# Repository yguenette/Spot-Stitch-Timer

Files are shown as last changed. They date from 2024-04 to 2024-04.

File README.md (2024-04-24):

# Spot-Stitch-Timer
Spot and Stitch Timer is a module to control the Miller Multimatic 215 Welder

## The module

To help weld thin metal (20, 22 and 24 AWG) and to maintain a minimal heat affected zone, it is important to find the right combination of voltage, WFS (wire feed speed), distance and trigger "on" time to eliminate the possibility of through holes or under welding. The key is to practice on similar metal pieces on a bench in ideal conditions where experimentation is possible. The voltage and WFS are pre-determined by the welder and can be fine tuned by the user - they are dialed in. Once programmed, these values will remain constant until they are changed. The nozzle distance to object is controllable by the user and more or less repeatable. The last variable (trigger ON time) is harder to reproduce since the position, the posture and the shear number of welds can make it difficult to maintain/repeat consistently. This is where a spot timer comes in. Once programmed with a spot ON time, it will remain the same until changed by the user. Having the flexibility of adding a delay time before the spot weld ON time will allow the user to press/release the trigger, before the weld starts and have a more stable position for the weld.

The spot/stitch timer module controls the welder with very specific welding time that will help with reproducibility of the welds. By dialing in the voltage, WFS, distance and weld time, we are closer to achieving repeatable welds.

This module (Raspberry Pi Pico and a 4 channels relay board) is packaged in a 3D printed box. This box sits inside the welder - in the same compartment as the wire spool - between the trigger torch and the welder. This module has 4 mode of operations. They are:

	1.  **Unpowered-Normal** : In this mode (default) the torch's trigger is passed through to the welder.
	2.  **Powered-Normal** : In this mode (default) the torch's trigger is passed through to the welder.
	3.  **Powered-Spot** : In this mode, the torch's trigger is isolated from the welder and sensed by the spot/stitch timer module. The Spot weld-time is programmable: delay and the spot weld ON time are specified. Each time the trigger is pressed/released, the module will create a combination Delay/Spot weld ON sequence;
	4.  **Powered-Stitch** : In this mode, the torch's trigger is isolated from the welder and sensed by the spot/stitch timer module. The Stitch ON/OFF weld-time is programmable: delay and the stitch weld ON/OFF time are specified. This sequence weld-ON/weld-OFF is repeated until the trigger is pressed/released again.

## The control software (interface):

When powered, the spot/stitch timer module will default to normal mode. The module can be controlled via Bluetooth using a android smartphone. The Android program used to communicate with the spot/stitch timer module is called: Serial Bluetooth Terminal, and is available through the app store.

Once connected, there are 6 pre-program functions and 2 commands supported. 

The 6 pre-programmed functions are:

	1.  **normal** : This programs the powered module to return to normal mode;
	2.  **mode?** : This sends a command to the module asking to report the present mode of operation. The possible response is:
		a. normal;
		b. spot;
		c. stitch;
	3.  **prog?** : This sends a command to the module asking to report the programmed delay, On and Off (only for stitch mode) for both spot and stitch modes;
	4.  **temp?** : asking the raspberry pi pico for its internal temperature. Normal temperature that I have seen range from 26C to 39C. The specification for the pico is : Max = +70C, Min = -20C.
	5.  **count?** : This reports the number of spot welds performed in this session and the number of stitch welds in this session;
	6.  **help** : reports the format of the 2 additional commands. They are:
		a. Spot delay ON
		b. Stitch delay ON OFF

The 2 commands supported are:

	1. spot <delay> <ON>
	2. stitch <delay> <ON> <OFF>

Looking at the Serial Bluetooth Terminal application, we can connect with the module by pressing the symbol on the second line from the top, third from the left.

The spot/stitch supported commands are typed on the bottom line. The command is send by pressing the icon on the right side of that line.

Screenshot_20240423_170638_Serial Bluetooth Terminal

## The final product



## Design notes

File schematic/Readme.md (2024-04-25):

# Schematic directory structure

Tool used for the schematic capture is KiCad

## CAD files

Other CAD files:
3D-Print-files/Cover FINAL.f3d
3D-Print-files/Languette Light FINAL.f3d
3D-Print-files/box_85x85mm FINAL (CURRENT).f3d
3D-Print-files/protective plate FINAL.f3d

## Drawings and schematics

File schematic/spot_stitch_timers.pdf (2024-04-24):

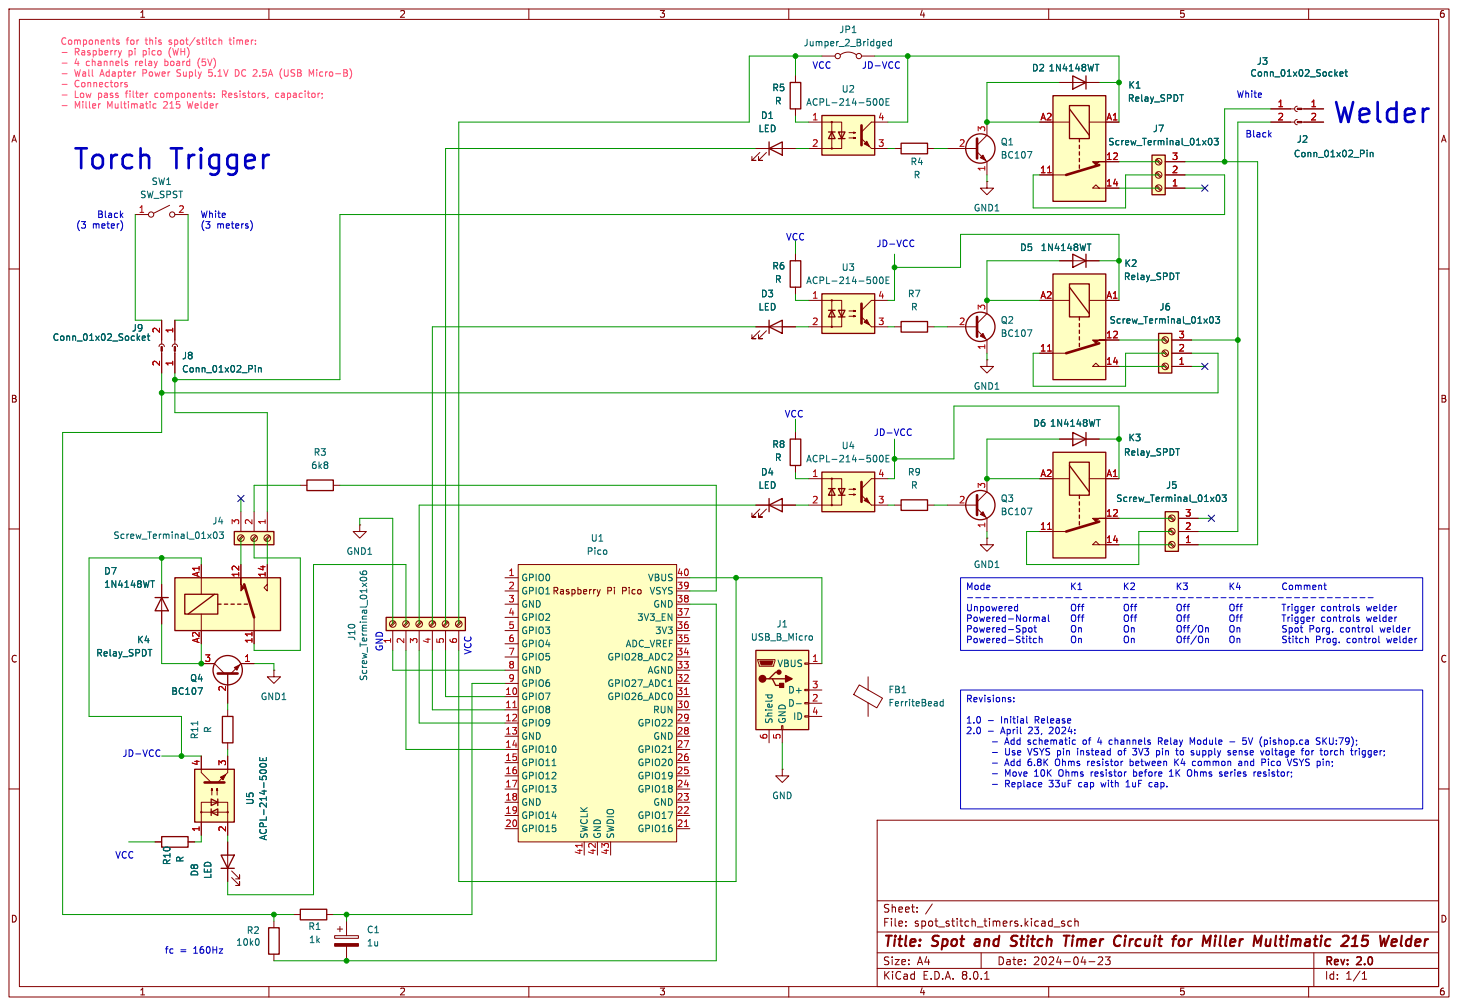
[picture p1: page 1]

- Wall Adapter Power Suply 5.1V DC 2.5A (USB Micro-B)
- Connectors
Torch Trigger

Id: 1/1 Title: Spot and Stitch Timer Circuit for Miller Multimatic 215 Welder File: spot_stitch_timers.kicad_sch Sheet: /

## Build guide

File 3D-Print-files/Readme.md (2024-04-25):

# Description:

directory structure added for the 3D printed files.

Tool used: Fusion360

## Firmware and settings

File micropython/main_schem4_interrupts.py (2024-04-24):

#-------------------
# YAG:
#
# Code to start and monitor the Bluetooth LE (BT) function and monitor the welder trigger.
#   At the time of this writing (March 2024), the dual core functionality was
#   attempted but not successful while using BT. It was however dual core was functional while using simple
#   functions like LED blinking and counter exercises.
#
# All programs are modified via the BT interface. The Android application that I used is called:
#
#   Serial Bluetooth Terminal
#
#
# The steps in this program are:
#
#	1) Initialize the relays so that the circuit operates in "Normal" mode by default;
#       To be clear, after further investigation of bouncing with the Miller torch
#       - pressing the trigger causes between 11 and 15 bounces with a duration of worst case,
#       seen of 235ms (with 4.7kOhms pull-down), while the release of the trigger causes very
#       little bounces at all.
#       In the 'normal' mode, I decided to bypass the controller altogether and passthru the
#       miller trigger directly to the welder. Note that the welder likely has (internally)
#       a debouncing circuit. In this mode the relays are all in their OFF position.
#	2) When the trigger is activated, the program will determine if the mode of operation is:
#		a) NORMAL - trigger passthru directly to welder;
#		b) SPOT - trigger on/off is determined by the spot welder programmed duration;
#		c) STITCH - trigger on/off is determined by the stitch programmed ON time followed by
#			the programmed OFF time - repeat as long as the trigger remains ON.
#
# If the microcontroller is un-powered, the relays will be positioned to allow the trigger to
#   be passed on to the welder.
#
# 1.0.0 - Initial version. March 26, 2024
#			- Allow bluetooth communication
#
# 5.0.0 - Now using V3 of the schematic - see green book for more details.
#       - Two (2) major changes done to the schematic:
#           - 1) Relay 3 was simplified so that Common pole and NO (Normally Open) pole are
#                  connected to the outputs of the relay 1 and 2 (Normally Closed poles).
#
#           - 2) Relay 4 is now used to disconnected the 'white' trigger wire from the pin 4 of
#                  the RPI-PICO. When the RPI-PICO is un-powered, the voltage at that pin is 17.7V
#                  That has the potential to destroy the PICO.
#
# 6.0.0 - Now using version 4 of the schematic. In this version, the "pwr_3v3_meas" pin is now connected
#         to the 3V3 power pin (3.3V). This means that wire on pin 4 is moved to pin 36.
#         Also, pin 34 is now jumpered to GND (pin 38).
#         From a programming point of view, these 2 pins (GPIO28 (pin 34) and GPIO2 (pin 4)) are now
#         GPIO input pins.

#
# future work:
#
#-------------------------------
# Import necessary modules
import _thread, utime
from machine import Pin, mem32
import bluetooth
from ble_simple_peripheral import BLESimplePeripheral

bounce_delay = 0.1
relay_switching = 0.1

# Backend GPIO pin definitions
# --------------------------------
relay_1 = machine.Pin(7,machine.Pin.OUT) #Relay 1 control. Turn ON by forcing 0V.
relay_2 = machine.Pin(8,machine.Pin.OUT) #Relay 1 control. Turn ON by forcing 0V.
relay_3 = machine.Pin(9,machine.Pin.OUT) #Relay 1 control. Turn ON by forcing 0V.
relay_4 = machine.Pin(10,machine.Pin.OUT) #Relay 1 control. Turn ON by forcing 0V.

# Relay control section (initializtion/default settings). Backend:
#------------------------------------------------------------------
# Control the GPIO pins to the correct default states
led_state = 0 # PICO green LED. Default state is OFF
relay_1_state = 0 # Relay 1 control state. Default is OFF - used for the passthru of the white wire
relay_2_state = 0 # Relay 2 control state. Default is OFF - used for the passthru of the black wire
relay_3_state = 0 # Relay 3 control state. Default is OFF - this relay is only controlled during SPOT and STITCH modes.
relay_4_state = 0 # Relay 4 control state. Default is OFF

relay_1.value(not relay_1_state)
relay_2.value(not relay_2_state)
relay_3.value(not relay_3_state)
relay_4.value(not relay_4_state)

utime.sleep(relay_switching) # Wait for the relays to settle.

# Frontend GPIO pins to use for the switch sensing
#---------------------------------------------------------
#This output is used to drive a fixed level. Between this output (pwr_3v3_meas) and the sensing input (sw_in), there is relay4 (default off)
#   and the trigger of the welder.
# pwr_3v3_meas = machine.Pin(2,  machine.Pin.IN) #This is now connected to 3.3V
sw_in    = machine.Pin(6,  machine.Pin.IN) #other side of the switch. Input. Pull-up of 4.7K provided externally. The other side of this PD is another GPIO (28)
# gnd_meas = machine.Pin(28, machine.Pin.IN) # GPIO pin used as a GND when in SPOT and STITCH modes only. Else input floating,
sw_in.irq(handler=None)  # disable interrupt during the switching of relay4. It creates an interrupt.

# Temperature sensor initialization
#------------------------------------------
adcpin = 4
sensor = machine.ADC(adcpin)


#Global variables:
normal = 1
spot = 0
spot_delay = 0
spot_time = 0
stitch = 0
stitch_delay = 0
stitch_ON = 0
stitch_OFF = 0
interrupt_flag = 0
spot_counter = 0
stitch_counter = 0

# Bluetooth Inititalization:
#----------------------------------------
# Create a Bluetooth Low Energy (BLE) object
ble = bluetooth.BLE()

# Create an instance of the BLESimplePeripheral class with the BLE object
sp = BLESimplePeripheral(ble)


# GPIO output drive coding:
#------------------------------------
PADS_BANK0_BASE     = 0x4001C000

PAD_GPIO            = PADS_BANK0_BASE + 0x04 # Add (pin * 4)
PAD_GPIO_MPY        = 4

PAD_DRIVE_BITS      = 4 # 0=2mA, 1=4mA, 2=8mA, 3=12mA   Default=1, 4mA drive

def SetPinDriveStrength(pin, mA):
  adr = PAD_GPIO + PAD_GPIO_MPY * pin
  mem32[adr] &= 0xFFFFFFFF ^ ( 0b11 << PAD_DRIVE_BITS)
  if   mA <= 2 : mem32[adr] |= 0b00 << PAD_DRIVE_BITS
  elif mA <= 4 : mem32[adr] |= 0b01 << PAD_DRIVE_BITS
  elif mA <= 8 : mem32[adr] |= 0b10 << PAD_DRIVE_BITS
  else         : mem32[adr] |= 0b11 << PAD_DRIVE_BITS


#This is code that will support interruptions for the sw_in pin.
#----------------------------------------------------------------
def callback(pin):
    global normal
    global spot
    global stitch
    global interrupt_flag
    
    # We should never see a trigger in this mode - mainly because relay4 is open which means there is no contact between GPIO input and output.
    if spot == 1:
        interrupt_flag = 1 # used most often
    elif stitch == 1:
        interrupt_flag = 1 # used most often
    else: # only normal remaining - which should never happen because relay4 is open...
        interrupt_flag = 0


# This is the code to handle the different modes once a trigger is detected
# -------------------------------------------------------------------------
def trigger():
#     import utime
    global normal
    global spot
    global spot_delay
    global spot_time
    global stitch
    global stitch_delay
    global stitch_ON
    global stitch_OFF
    global relay_1_state
    global relay_2_state
    global relay_3_state
    global relay_4_state
    global interrupt_flag
    global spot_counter
    global stitch_counter
    global relay_switching
#
    # NORMAL Section
    #---------------
    if normal == 1:      # ...and the mode is normal. Trigger ON/OFF programs welder ON/OFF.
        # should not happen because relay4 is open and this means that the pwr_3v3_meas cannot drive a level 1 through the trigger.
        sp.send('YAG_ERROR: No Trigger in NORMAL mode\r\n')
        

    # SPOT TIMER SECTION
    #-------------------
    elif spot == 1:
        
        # Wait a finite amount of time for the trigger to be released
        # to make the welding more comfortable.
        #------------------------------------------------------------
        utime.sleep(spot_delay)
        spot_counter = spot_counter + 1
        
        # control the relay to simulate the trigger being pressed:
        #---------------------------------------------------------
        relay_3_state = 1
        relay_3.value(not relay_3_state) # turn relay 3 ON
        # wait for switching
        utime.sleep(relay_switching)  # Wait relay_switching before continuing.

        utime.sleep(spot_time) # wait the specified anmount of time with simulated trigger pressed.
        
        # control the relay to simulate the trigger being released:
        #----------------------------------------------------------
        relay_3_state = 0
        relay_3.value(not relay_3_state) # turn relay 3-4 OFF (open these 2 relays)
        # wait for switching
        utime.sleep(relay_switching)  # Wait relay_switching before continuing.
        
        # This is to cover the case where the trigger remains pressed....wait until it is
        #   released
        #--------------------------------------------------------------------------------
        while (sw_in.value() == 1): # trigger is still on.
            # do nothing. Wait it out until trigger is released. No other trigger will start a spot weld.
            pass
        utime.sleep(bounce_delay) # it will come out the 'while' only if the trigger was released.
        interrupt_flag = 0 # reset interrupt flag manually....
        
        
    elif stitch == 1:
        # Wait a finite amount of time for the trigger to be released
        # to make the welding more comfortable.
        #------------------------------------------------------------
        
        utime.sleep(stitch_delay)
        
        # first cycle run manually. This eliminates the need to account for any bouncing in the trigger.
        # At the end of this time, the trigger will have been stable - either ON or OFF.
        stitch_counter = stitch_counter + 1
        relay_3_state = 1
        relay_3.value(not relay_3_state) # turn relay 3 ON (close this relay)

        utime.sleep(relay_switching)  # Wait relay_switching before continuing.

        utime.sleep(stitch_ON) # wait the specified amount of time with the trigger ON
                
        interrupt_flag = 0 #reset this flag

        # control the relay to simulate the trigger being released:
        #----------------------------------------------------------
        relay_3_state = 0
        relay_3.value(not relay_3_state) # turn relay 3-4 OFF (open these 2 relays)

        utime.sleep(relay_switching)  # Wait relay_switching before continuing.
        
        # wait the amount of time for the trigger being released.
        utime.sleep(stitch_OFF)
        
        
        # dtermine the state of the trigger based on the level at the sw_in pin.
        #----------------------------------------------------------------------
        if (sw_in.value() == 1): # this means that the trigger is still on and the looping will continue until it is released.
                                # This is the case where the user wants to work in the mode where only one ON/OFF is used
                                # for the duration of thestitch mode.
                                
            # control the relay to simulate the trigger STILL being pressed:
            #---------------------------------------------------------------
            while (sw_in.value() == 1): # while the trigger is ON continue to ON/OFF the welder until released
                stitch_counter = stitch_counter + 1
                relay_3_state = 1
                relay_3.value(not relay_3_state) # turn relay 3-4 ON (close these 2 relays)

                utime.sleep(relay_switching)  # Wait relay_switching before continuing.

                utime.sleep(stitch_ON) # wait the specified amount of time with the trigger ON
                        
                # control the relay to simulate the trigger being released:
                #----------------------------------------------------------
                relay_3_state = 0
                relay_3.value(not relay_3_state) # turn relay 3-4 OFF (open these 2 relays)

                utime.sleep(relay_switching)  # Wait relay_switching before continuing.

                # wait the amount of time for the trigger being released.
                utime.sleep(stitch_OFF)
        
        elif (sw_in.value() == 0): # this means that the trigger was released in the first stitch cycle and to stop the cycles
                                    # from continuing, we need another trigger ON action to stop it.
            # control the relay to simulate the trigger was released previously:
            #---------------------------------------------------------------------
            while (interrupt_flag == 0): # repeat this loop until another interrupt is generated.
                stitch_counter = stitch_counter + 1
                relay_3_state = 1
                relay_3.value(not relay_3_state) # turn relay 3-4 ON (close these 2 relays)

                utime.sleep(relay_switching)  # Wait relay_switching before continuing.

                utime.sleep(stitch_ON) # wait the specified amount of time with the trigger ON
                        
                # control the relay to simulate the trigger being released:
                #----------------------------------------------------------
                relay_3_state = 0
                relay_3.value(not relay_3_state) # turn relay 3-4 OFF (open these 2 relays)

                utime.sleep(relay_switching)  # Wait relay_switching before continuing.

                # wait the amount of time for the trigger being released.
                utime.sleep(stitch_OFF)

        interrupt_flag = 0
        

def ReadTemperature():
 	adc_value = sensor.read_u16()
 	volt = (3.3/65535) * adc_value
 	temperature = 27 - (volt - 0.706)/0.001721
 	return round(temperature, 1)

def default_normal():
    # disable interrupt requests.
    
    relay_1_state = 0 # Relay 1 control state. Default is OFF - used for the passthru of the white wire
    relay_2_state = 0 # Relay 2 control state. Default is OFF - used for the passthru of the black wire
    relay_3_state = 0 # Relay 3 control state. Default is OFF - this relay is only controlled during SPOT and STITCH modes.
    relay_4_state = 0 # Relay 4 control state. Default is OFF

    # no interrupt needed for normal mode. Signal passthrough spot timer box.
    sw_in.irq(handler=None)  # disable interrupt during the switching of relay4. It creates an interrupt.

    relay_4.value(not relay_4_state) # turn off relay4 first to save the PICO input.
    relay_3.value(not relay_3_state)
    
    utime.sleep(relay_switching) # Wait for the relays to settle.
    
    relay_1.value(not relay_1_state)
    relay_2.value(not relay_2_state)

    utime.sleep(relay_switching) # Wait for the relays to settle.


def default_spot_stitch():
    # disable interrupt requests while switching around the relays configurations.
    
    relay_1_state = 1 # Relay 1 control state. Default is OFF - used for the passthru of the white wire
    relay_2_state = 1 # Relay 2 control state. Default is OFF - used for the passthru of the black wire
    relay_3_state = 0 # Relay 3 control state. Default is OFF - this relay is only controlled during SPOT and STITCH modes.
    relay_4_state = 1 # Relay 4 control state. Default is OFF

    relay_1.value(not relay_1_state)
    relay_2.value(not relay_2_state)
    relay_3.value(not relay_3_state)

    utime.sleep(relay_switching) # Wait for the relays to settle.
    
    sw_in.irq(handler=None)  # disable interrupt during the switching of relay4. It creates an interrupt.
    
    relay_4.value(not relay_4_state)

    utime.sleep(1) # Wait for the relays to settle.
    
    sw_in.irq(trigger=Pin.IRQ_RISING, handler=callback)

    
    
# Define a callback function to handle received data
def on_rx(data):
    global normal
    global spot
    global spot_delay
    global spot_time
    global stitch
    global stitch_delay
    global stitch_ON
    global stitch_OFF
    global led_state  # Access the global variable led_state
    global spot_counter
    global stitch_counter
    
#     print("Data received: ", data)  # Print the received data
    s_data = data.decode('ascii')
    s_data = s_data.replace("\r\n","")
#     print("String Data received: ", s_data)  # Print the received data
    if data == b'normal\r\n':
        normal = 1
        spot = 0
        stitch = 0
        
        # disable irq in this mode.
        default_normal()
        
    elif (s_data.find('spot ')!=-1):
        #
        x = s_data.split(" ")
        tmp_delay = (x[1])
        tmp = (x[2])
        
        normal = 0
        spot = 1
        spot_delay = float(tmp_delay)
        spot_time = float(tmp)
        stitch = 0
        default_spot_stitch()


    elif (s_data.find('stitch ')!=-1):
        #
        x = s_data.split(" ")
        tmp_delay_stitch = (x[1])
        tmp1 = (x[2])
        tmp2 = (x[3])
        
        normal = 0
        spot = 0
        stitch = 1
        stitch_delay = float(tmp_delay_stitch)
        stitch_ON = float(tmp1)
        stitch_OFF = float(tmp2)
        default_spot_stitch()

    elif (s_data.find('mode?') != -1): # match
        if normal == 1:
            sp.send('normal\r\n')
        
        elif spot == 1:
            sp.send('spot\r\n')
            
        elif stitch == 1:
            sp.send('stitch\r\n')
        
    elif (s_data.find('program?') != -1): # match
        data_new = 'spot delay: '+ str(spot_delay) + ', ON: ' + str(spot_time) + '\r\n'
        sp.send(data_new)
        data_new = 'stitch delay: '+ str(stitch_delay) + ', ON: ' + str(stitch_ON)+ ', OFF: ' + str(stitch_OFF) + '\r\n'
        sp.send(data_new)
        
    elif (s_data.find('temp?') != -1):
        temperature = str(ReadTemperature()) + '\r\n'
        sp.send(temperature)
        
    elif (s_data.find('counters?') != -1):
        data_new = 'spot counter: '+ str(spot_counter) + ', stitch counter: ' + str(stitch_counter) + '\r\n'
        sp.send(data_new)

    elif (s_data.find('help') != -1):
        data_new = 'spot <delay> <ON time>' + '\r\n'
        sp.send(data_new)
        data_new = 'stitch <delay> <ON time> <OFF time>' + '\r\n'
        sp.send(data_new)

    else:
        sp.send('YAG_ERROR: wrong command\r\n')
        



while True:
    if sp.is_connected():  # Check if a BLE connection is established
        sp.on_write(on_rx)  # Set the callback function for data reception

    if (interrupt_flag == 1 and normal == 0):   # trigger is pressed
        trigger()
        
#     if (sw_in.value() == 1 and normal == 0):   # trigger is pressed
#         trigger()

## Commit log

2024-04-24 Add files via upload
    Schematic capture file using KiCad free software (Version Project 8.0)
    [spot_stitch_timers.kicad_sch]
2024-04-24 Add files via upload
    PDF file of the latest schematic
2024-04-24 Add files via upload
    The 3D design files (from Fusion360) for the design of the box and support for the Raspberry Pi Pico board and the 4 channels relay board.
    There are 4 pieces to print. They are:
    1) the base box;
    2) the cover;
    3) the 'languette' for the Pico;
    4) the protective plate between the case and the relay board.
    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
    [Cover FINAL.f3d, Languette Light FINAL.f3d, box_85x85mm FINAL (CURRENT).f3d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]
2024-04-24 Update README.md
    Added the picture of the finished module when in the welder
2024-04-25 Create schematic
2024-04-25 Create Readme.md
    Schematic directory structure added
2024-04-25 Add files via upload
    Initial release in directory structure
    [spot_stitch_timers.kicad_sch]
2024-04-25 Delete Cover FINAL.f3d
    remove and add to directory structure
    [Cover FINAL.f3d]
2024-04-25 Delete Languette Light FINAL.f3d
    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
    [Languette Light FINAL.f3d]
2024-04-25 Delete box_85x85mm FINAL (CURRENT).f3d
    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
    [box_85x85mm FINAL (CURRENT).f3d]
2024-04-25 Delete protective plate FINAL.f3d
    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
    [protective plate FINAL.f3d]
2024-04-25 Delete spot_stitch_timers.kicad_sch
    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
    [spot_stitch_timers.kicad_sch]
